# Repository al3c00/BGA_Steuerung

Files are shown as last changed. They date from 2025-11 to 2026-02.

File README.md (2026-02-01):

# BGA_Steuerung

## Übersicht:

Dieses Repository enthält Platine-Daten und Software zur Steuerung und Überwachung der Substratflüsse einer landwirtschaftlichen Biogasanlage. Angesteuert werden elektrische Motoren (Pumpen und Mischmotoren) mitels Schützrelais sowie pneumatisch gesteuerte Schieber mit einem 24V 5/2 Pneumatikventil.

## Funktion:

## Schnittstellen der Steuerungsplatine:

+ 24 Digitale Inputs für NPN-Sensoren (Signal aktiv wenn auf Masse gezogen)
+ 6 Analoge Inputs (Stromschleife 4-20mA)
+ 2 Analoge Inputs (0-5v)
+ 16 Digitale Outputs
+ UART, SPI, I2C, drahtlose Kommunikationsmöglichkeiten des Raspberry Pi 4
  
## Steuerung der Anlage:
### Sequenzen für Steuerung:
Das Programm lädt Sequenzen, die zu einem bestimmten Zeitpunkt abgespielt werden sollen. Der Benutzer ist frei in der Programmierung der Sequenzen. Diese werden in einer .txt-Datei gespeichert und bei allfälligem Neustart des Programms wieder aufgerufen. Jede Funktion wird in einem eigenen Thread ausgeführt
Es können folgende Funktionen verwendet werden:
|Funktionsname|Beschrieb|Parameter_int1|Parameter_int2|Parameter_string1|Parameter_string2|
|---|---|---|---|---|---|
|WAIT_MS|Stoppt die Ausführung der Sequenz indem der Thread mittels std::this_thread::sleep_for angehalten wird|Wartezeit in Millisekunden int|-|-|-|
|WAIT_S|Stoppt die Ausführung der Sequenz indem der Thread mittels std::this_thread::sleep_for angehalten wird|Wartezeit in Sekunden int|-|-|-|
|WAIT_MIN|Stoppt die Ausführung der Sequenz indem der Thread mittels std::this_thread::sleep_for angehalten wird|Wartezeit in Minuten int|-|-|-|
|WAIT_H|Stoppt die Ausführung der Sequenz indem der Thread mittels std::this_thread::sleep_for angehalten wird|Wartezeit in Stunden int|-|-|-|
|WAIT_UNTIL|Stoppt die Ausführung der Sequenz bis zu einer gewissen Tageszeit (HHMM). Der Thread wird mit std::this_thread::sleep_for angehalten und es wird alle 30 Sekunden überprüft, ob die Uhrzeit erreicht worden ist|Tageszeit Stunde int|Tageszeit Minute int|-|-|
|JUMP_TO|Springt zu einer bestimmten Position in der Sequenz und fährt dort weiter|Zielposition (0 bis n)|-|-|-|
|PROGRESS_IF_1|Die Ausführung der Sequenz wird angehalten bis eine bestimmte Bedingung erfüllt ist an **einem** Input erfüllt ist|int_Zustand, der zu erfüllen ist|-|Input, der abgefragt wird|-|
|PROGRESS_IF_2|Die Ausführung der Sequenz wird angehalten bis eine bestimmte Bedingung erfüllt ist an **zwei** Inputs erfüllt ist (siehe HW_Con::getDoubleInputState|int_Zustand, der zu erfüllen ist|-|Input, der abgefragt wird|Input, der abgefragt wird|
|GET_DIGITAL_INPUT|Der aktuelle Zustand eines digitalen Inputs wird abgefragt|-|-|Input, der abgefragt wird|-|
|GET_DOUBLE_DIGITAL_INPUT|Die Funktion "getDoubleInputState" wird verwendet, um die Sensorwerte eines mechanischen Bauteils, dass Stellung An und Aus überwacht (nicht nur eine von beiden) zu überprüfen|-|-|Input1, der abgefragt wird|Input2, der abgefragt wird|
|GET_ANALOG_INPUT|Der aktuelle Zustand eines analogen Inputs wird abgefragt|-|-|Input, der abgefragt wird|-|
|SET_DIGITAL_OUTPUT|Der Zustand eines digitalen Outputs wird unabhängig von seinem aktuellen Zustand gesetzt|Zustand, der gesetzt werden soll (0/1, eigentlich Bool)|-|Output, der gesetzt werden soll|-|
|SWITCH_DIGITAL_OUTPUT|Der Zustand eines digitalen Outputs wird abhängig von seinem aktuellen Zustand ins Gegenteil gesetzt|-|-|Output, der gesetzt werden soll|-|
|NOT_DEFINED|Wird verwendet, um Fehler abzufangen und die struct zu konstruieren

Die Funktionen in der .txt-Datei nutzen folgende Syntax:
|Objekt|Beschrieb|
|---|---|
|#Sequencename|Name der Sequenz. Dieser wird im Quellcode für die Zuordnung an verschiedensten Stellen benutzt.| 
|"{"|Markiert den Beginn der Sequenz|
|Funktionsname(Parameter1, ev. Parameter2)|Siehe die oben beschriebenen Funktionen oder im Quellcode Sequence_Handler.h|
|"}"|Markiert das Ende der Sequenz|

Alle Sequenzen werden in derselben Datei gespeichert.

## Software:
### Allgemein:
Das Programm läuft auf einem Raspberry Pi 4, welcher mittel I2C mit den IO-Expandern auf der Platine kommuniziert. Die Kommunikation übernimmt eine Klasseninstanz von HW_Con. Die grafische Darstellung übernimmt die Klasse GUI, für z.B.unterschiedliche Ebenen können mehrere Instanzen erzeugt werden. Für das Rendering wird SDL2 genutzt. Es wird auf eine Abstrahierung des Quellcodes geachtet, viele Positionen der Elemente auf dem Display können in der dazugehörigen .txt-Datei angepasst und in der Software während Laufzeit neu geladen werden.

### GUI:
Es existiert mindestens eine Instaz der Klasse GUI. Damit können Bilder geladen und angezeigt und Text ausgegeben werden. Alle grafischen Elemente werden in einer std::map mit einem string-key referenziert. Es lassen sich vordefinierte Positionen in einem .txt-Dokument speichern und laden.

### HW_Con:
Von dieser Klasse darf nur eine Instanz erzeugt werden. Mittels I2C kommuniziert der PI mit den PCF8574 auf der Platine. Die einzelnen Inputs/Outputs sind mit ihren 7-Bit I2C Adressen der Chips sowie dem Port mit string-Namen in einer Map referenziert. *Beispiel: D_Out_0 --> dec35,p0.* Für jeden Input/Output existiert eine struct "IO_Object". Die Inputs werden im Main-Loop regelmässig neu abgefragt. Bei den Outputs wird der **Soll-Zustand** in dieser struct gespeichert und übermittelt. Der Ist-Zustand kann nicht abgefragt werden.

### Sequence_Handler:
Von dieser Klasse darf nur eine Instanz erzeugt werden. Sie lädt, speichert und organisert alle Sequenzen und überwacht deren Ausführung und gegebenenfalls Bearbeitung.

## Weiteres
Verbesserungspotenzial:
+ GND Pins bei I2C und UART Terminals vergessen
+ Sicherheit der digitalen Outputs verbessern (z.B.: blockieren der Stromversorgung aller Relais bis zum Zeitpunkt der explizit gewünschten Freigabe
+ Schöneres Layout der Platine
+ Aufbauposition des Raspberry optimieren
+ Pin Header besser zu Montageposition des RPI anpassen
+ Diverses mehr

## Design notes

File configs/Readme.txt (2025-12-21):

Sequences
WAIT(int-->wait time in ms);
PROGRESS_IF_1(int-->should_be_state, string-->input to check);
PROGRESS_IF_2(int-->should_be_state, string-->input one to check, string-->input two to check);
SWITCH_DIGITAL_OUTPUT(string-->output to switch);

//Finish lines with ;

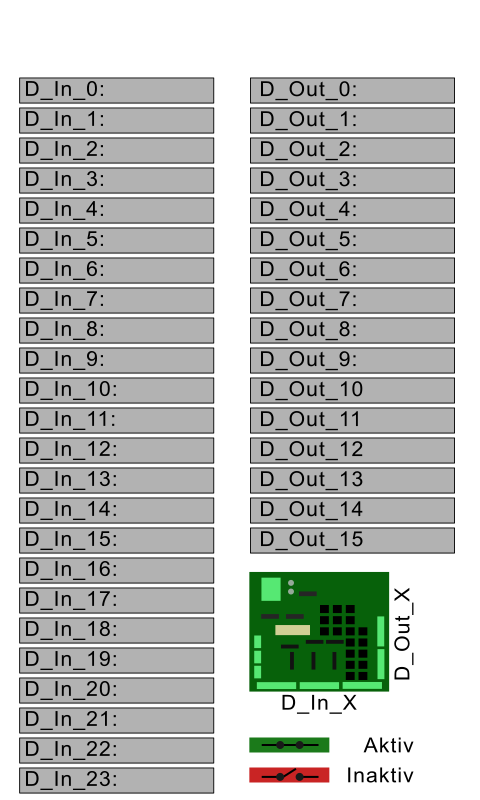
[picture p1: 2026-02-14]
resource/schema_IO_v1.png

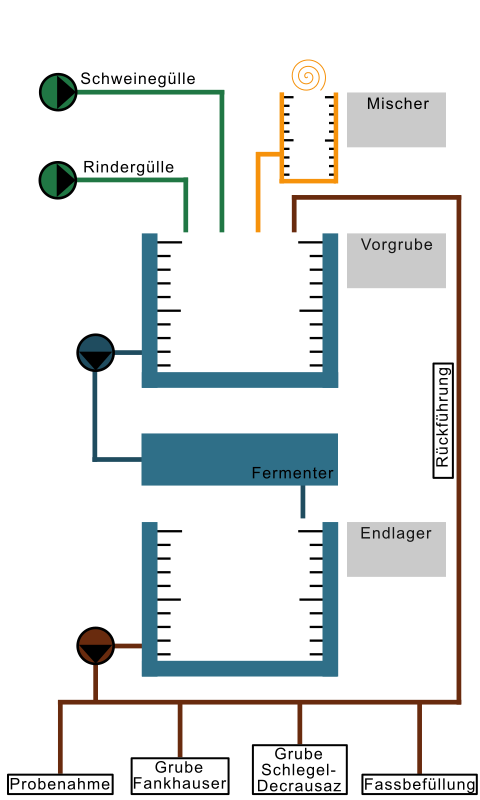
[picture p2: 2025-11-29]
resource/schema_bga_v3.png

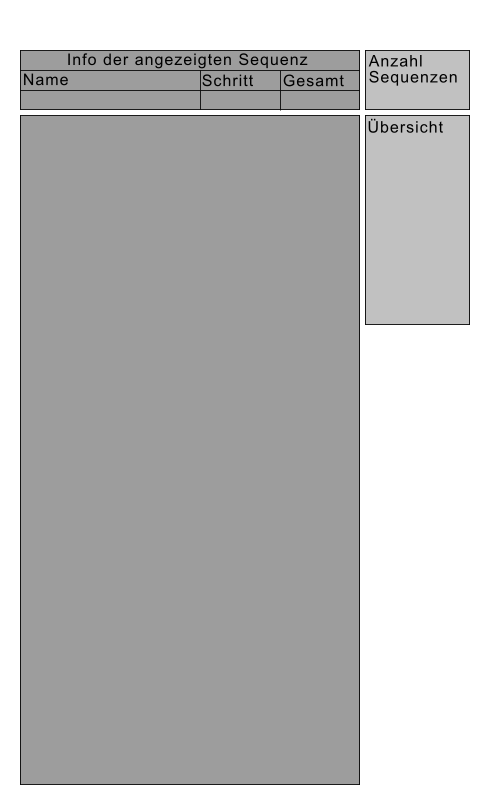
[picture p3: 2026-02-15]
resource/Sequenzuebersicht.png

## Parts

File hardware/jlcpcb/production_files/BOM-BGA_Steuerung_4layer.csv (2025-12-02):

Comment | Designator | Footprint | LCSC | Quantity
0.1uF | C10,C11,C12,C13,C14,C15,C34 | C_0603_1608Metric | C1590 | 7
0.1uf | C16,C17,C18,C19,C20,C21,C22,C23,C24,C25,C26,C27,C28,C29,C30,C31,C32,C33 | C_0603_1608Metric | C1590 | 18
1.8k | R81,R87,R91,R94,R96,R98 | R_0603_1608Metric | C4177 | 6
100nF | C35,C36,C37 | CP_Elec_4x5.4 | C271438 | 3
10k | R117,R118,R119,R120,R121,R122,R123,R124,R125,R126,R127,R128,R129,R130 | R_0603_1608Metric | C15401 | 14
10nF | C39,C40 | C_0603_1608Metric | C1589 | 2
10uF | C3 | C_Elec_4x5.4 | C3343 | 1
150 | R2,R4 | R_0603_1608Metric | C22808 | 2
1N5824 | D2,D3,D6 | D_A-405_P12.70mm_Horizontal | C508482 | 3
1k | R10,R12,R14,R16,R18,R20,R22,R29,R30,R31,R32,R33,R34,R37,R38,R45,R46,R47,R48,R49,R50,R53,R54,R8,R85,R86 | R_0603_1608Metric | C14676 | 26
200 | R100,R71,R72,R73,R74,R75,R99 | R_0603_1608Metric | C8218 | 7
220nF | C38,C41,C42,C43,C44 | C_0603_1608Metric | C1606 | 5
220uF | C6,C7,C9 | C_Elec_8x10.2 | C3340 | 3
250 | R79,R82,R84,R88,R90,R92 | R_0805_2012Metric | C2828827 | 6
2k | R55,R56,R57,R58,R59,R60,R61,R62,R63,R64,R65,R66,R67,R68,R69,R70 | R_0603_1608Metric | C22975 | 16
33uH | L1,L2,L3 | L_Chilisin_BMRF00101040 | C6364680 | 3
4.7k | R5,R6,R77,R78,R80,R83,R89,R93,R95,R97 | R_0603_1608Metric | C23162 | 10
470uF | C1,C2 | C_Elec_10x10.2 | C3351 | 2
500 | R1 | R_0805_2012Metric | C2828857 | 1
510 | R101,R102,R103,R104,R105,R106,R107,R108,R109,R11,R110,R111,R112,R113,R114,R115,R116,R13,R15,R17,R19,R21,R23,R24,R25,R26,R27,R28,R35,R36,R39,R40,R41,R42,R43,R44,R51,R52,R7,R9 | R_0603_1608Metric | C23193 | 40
680uF | C4,C5,C8 | CP_Elec_5x5.4 | C3337 | 3
75 | R3 | R_0603_1608Metric | C4275 | 1
LED_Green | D48,D49,D50,D53 | L_0603_1608Metric | C118334 | 4
LED_Green | D1,D4,D5,D7 | LED_0805_2012Metric | C84260 | 4
LED_Red | D51,D52,D54 | L_0603_1608Metric | C2286 | 3
Raspberry_Pi_4b_GPIO_Header | U4 | PinHeader_2x20_P2.54mm_Vertical | C3326996 | 1
TCA9406DCUR | U35 | VSSOP-8_2.3x2mm_P0.5mm | C840107 | 1
Conn_01x24_Socket | J5 | Connector PTSA 24Pos Pitch=2.5mm |  | 1
2N4401 | Q5 | TO-92_Inline_Wide_EBC |  | 1
2N4401 | Q2 | TO-92_Inline_Wide_EBC |  | 1
2N4401 | Q13 | TO-92_Inline_Wide_EBC |  | 1
4N35 | U28 | DIP-6_W7.62mm |  | 1
LED | D19 | D_0603_1608Metric |  | 1
LED | D58 | D_0603_1608Metric |  | 1
LED | D22 | D_0603_1608Metric |  | 1
LED | D65 | D_0603_1608Metric |  | 1
2N4401 | Q14 | TO-92_Inline_Wide_EBC |  | 1
Conn_01x01_Pin | J20 | PinHeader_1x01_P1.00mm_Vertical |  | 1
LED | D25 | D_0603_1608Metric |  | 1
LED | D28 | D_0603_1608Metric |  | 1
4N35 | U8 | DIP-6_W7.62mm |  | 1
Conn_01x16_Socket | J6 | 1989887 |  | 1
1N4148 | D44 | D_DO-35_SOD27_P7.62mm_Horizontal |  | 1
LED | D13 | D_0603_1608Metric |  | 1
TPS26610 | U42 | SOT-23-8 |  | 1
2N4401 | Q11 | TO-92_Inline_Wide_EBC |  | 1
4N35 | U9 | DIP-6_W7.62mm |  | 1
4N35 | U25 | DIP-6_W7.62mm |  | 1
Screw_Terminal_01x02 | J22 | 691137710002 |  | 1
LED | D12 | D_0603_1608Metric |  | 1
Heatsink | HS1 | Heatsink_TO-220_V6560W |  | 1
Conn_01x01_Pin | J19 | PinHeader_1x01_P1.00mm_Vertical |  | 1
AZ9571-1C-12DSE | K7 | RELAY6_AZ9571-1C-12DSE_AMZ |  | 1
1990009 | J15 | 1990009 |  | 1
2N4401 | Q15 | TO-92_Inline_Wide_EBC |  | 1
~ | U5 | DIP-16_W7.62mm |  | 1
4N35 | U11 | DIP-6_W7.62mm |  | 1
LED | D64 | D_0603_1608Metric |  | 1
LED | D69 | D_0603_1608Metric |  | 1
1990009 | J14 | 1990009 |  | 1
1N4148 | D36 | D_DO-35_SOD27_P7.62mm_Horizontal |  | 1
LM2596T-5 | U3 | TO-220-5_P3.4x3.7mm_StaggerOdd_Lead3.8mm_Vertical |  | 1
LED | D14 | D_0603_1608Metric |  | 1
LED | D16 | D_0603_1608Metric |  | 1
TPS26610 | U39 | SOT-23-8 |  | 1
LED | D31 | D_0603_1608Metric |  | 1
1N4148 | D35 | D_DO-35_SOD27_P7.62mm_Horizontal |  | 1
AZ9571-1C-12DSE | K12 | RELAY6_AZ9571-1C-12DSE_AMZ |  | 1
LED | D26 | D_0603_1608Metric |  | 1
Conn_01x01_Pin | J21 | PinHeader_1x01_P1.00mm_Vertical |  | 1
1990009 | J13 | 1990009 |  | 1
4N35 | U19 | DIP-6_W7.62mm |  | 1
AZ9571-1C-12DSE | K13 | RELAY6_AZ9571-1C-12DSE_AMZ |  | 1
2N4401 | Q9 | TO-92_Inline_Wide_EBC |  | 1
1N4148 | D40 | D_DO-35_SOD27_P7.62mm_Horizontal |  | 1
1990009 | J16 | 1990009 |  | 1
LED | D21 | D_0603_1608Metric |  | 1
AZ9571-1C-12DSE | K2 | RELAY6_AZ9571-1C-12DSE_AMZ |  | 1
LED | D67 | D_0603_1608Metric |  | 1
LED | D29 | D_0603_1608Metric |  | 1
~ | U31 | DIP-16_W7.62mm |  | 1
Conn_01x01_Pin | J18 | PinHeader_1x01_P1.00mm_Vertical |  | 1
Heatsink | HS2 | Heatsink_TO-220_V6560W |  | 1
4N35 | U12 | DIP-6_W7.62mm |  | 1
LED | D68 | D_0603_1608Metric |  | 1
~ | U33 | DIP-16_W7.62mm |  | 1
2N4401 | Q4 | TO-92_Inline_Wide_EBC |  | 1
1N4148 | D33 | D_DO-35_SOD27_P7.62mm_Horizontal |  | 1
TPS26610 | U43 | SOT-23-8 |  | 1
1N4148 | D34 | D_DO-35_SOD27_P7.62mm_Horizontal |  | 1
AZ9571-1C-12DSE | K10 | RELAY6_AZ9571-1C-12DSE_AMZ |  | 1
AZ9571-1C-12DSE | K9 | RELAY6_AZ9571-1C-12DSE_AMZ |  | 1
1N4148 | D37 | D_DO-35_SOD27_P7.62mm_Horizontal |  | 1
1N4148 | D46 | D_DO-35_SOD27_P7.62mm_Horizontal |  | 1
~ | U44 | DIP-16_W7.62mm |  | 1
4N35 | U6 | DIP-6_W7.62mm |  | 1
LM2596T-3.3 | U2 | TO-220-5_P3.4x3.7mm_StaggerOdd_Lead3.8mm_Vertical |  | 1
2N4401 | Q12 | TO-92_Inline_Wide_EBC |  | 1
LED | D27 | D_0603_1608Metric |  | 1
Conn_01x01_Pin | J23 | PinHeader_1x01_P1.00mm_Vertical |  | 1
ADS1115IDGSR | U36 | TSSOP-10_3x3mm_P0.5mm |  | 1
1N4148 | D43 | D_DO-35_SOD27_P7.62mm_Horizontal |  | 1
LED | D10 | D_0603_1608Metric |  | 1
LED | D61 | D_0603_1608Metric |  | 1
LED | D66 | D_0603_1608Metric |  | 1
AZ9571-1C-12DSE | K3 | RELAY6_AZ9571-1C-12DSE_AMZ |  | 1
LED | D17 | D_0603_1608Metric |  | 1
4N35 | U18 | DIP-6_W7.62mm |  | 1
LED | D18 | D_0603_1608Metric |  | 1
LED | D15 | D_0603_1608Metric |  | 1
1N4148 | D41 | D_DO-35_SOD27_P7.62mm_Horizontal |  | 1
2N4401 | Q7 | TO-92_Inline_Wide_EBC |  | 1
~ | U34 | DIP-16_W7.62mm |  | 1
1N4148 | D38 | D_DO-35_SOD27_P7.62mm_Horizontal |  | 1
4N35 | U21 | DIP-6_W7.62mm |  | 1
AZ9571-1C-12DSE | K11 | RELAY6_AZ9571-1C-12DSE_AMZ |  | 1
LED | D11 | D_0603_1608Metric |  | 1
AZ9571-1C-12DSE | K1 | RELAY6_AZ9571-1C-12DSE_AMZ |  | 1
2N4401 | Q8 | TO-92_Inline_Wide_EBC |  | 1
4N35 | U14 | DIP-6_W7.62mm |  | 1
4N35 | U16 | DIP-6_W7.62mm |  | 1
Conn_01x24_Socket | J3 | Connector PTSA 24Pos Pitch=2.5mm |  | 1
1990009 | J11 | 1990009 |  | 1
4N35 | U17 | DIP-6_W7.62mm |  | 1
LED | D59 | D_0603_1608Metric |  | 1
2N4401 | Q16 | TO-92_Inline_Wide_EBC |  | 1
~ | U22 | DIP-16_W7.62mm |  | 1
ADS1115IDGSR | U37 | TSSOP-10_3x3mm_P0.5mm |  | 1
Power_Rasperry | J2 | TerminalBlock_MetzConnect_Type055_RT01502HDWU_1x02_P5.00mm_Horizontal |  | 1
Screw_Terminal_01x02 | J17 | 691137710002 |  | 1
AZ9571-1C-12DSE | K14 | RELAY6_AZ9571-1C-12DSE_AMZ |  | 1
1N4148 | D47 | D_DO-35_SOD27_P7.62mm_Horizontal |  | 1
1N4148 | D32 | D_DO-35_SOD27_P7.62mm_Horizontal |  | 1
AZ9571-1C-12DSE | K5 | RELAY6_AZ9571-1C-12DSE_AMZ |  | 1
LED | D30 | D_0603_1608Metric |  | 1
1N4148 | D42 | D_DO-35_SOD27_P7.62mm_Horizontal |  | 1
4N35 | U20 | DIP-6_W7.62mm |  | 1
Conn_01x01_Pin | J24 | PinHeader_1x01_P1.00mm_Vertical |  | 1
1N4148 | D39 | D_DO-35_SOD27_P7.62mm_Horizontal |  | 1
4N35 | U29 | DIP-6_W7.62mm |  | 1
2N4401 | Q6 | TO-92_Inline_Wide_EBC |  | 1
4N35 | U15 | DIP-6_W7.62mm |  | 1
4N35 | U23 | DIP-6_W7.62mm |  | 1
2N4401 | Q1 | TO-92_Inline_Wide_EBC |  | 1
4N35 | U7 | DIP-6_W7.62mm |  | 1
1990012 | J10 | 1990012 |  | 1
Conn_01x24_Socket | J4 | Connector PTSA 24Pos Pitch=2.5mm |  | 1
4N35 | U30 | DIP-6_W7.62mm |  | 1
2N4401 | Q3 | TO-92_Inline_Wide_EBC |  | 1
LED | D70 | D_0603_1608Metric |  | 1
TPS26610 | U38 | SOT-23-8 |  | 1
4N35 | U27 | DIP-6_W7.62mm |  | 1
1N4148 | D45 | D_DO-35_SOD27_P7.62mm_Horizontal |  | 1
AZ9571-1C-12DSE | K6 | RELAY6_AZ9571-1C-12DSE_AMZ |  | 1
1990012 | J9 | 1990012 |  | 1
4N35 | U24 | DIP-6_W7.62mm |  | 1
4N35 | U10 | DIP-6_W7.62mm |  | 1
Heatsink | HS3 | Heatsink_TO-220_V6560W |  | 1
LED | D8 | D_0603_1608Metric |  | 1
LED | D57 | D_0603_1608Metric |  | 1
Screw_Terminal_0,5-6,0mm2 | J1 | PCB_terminal_block_1932588 |  | 1
4N35 | U26 | DIP-6_W7.62mm |  | 1
LED | D23 | D_0603_1608Metric |  | 1
TPS26610 | U41 | SOT-23-8 |  | 1
LED | D60 | D_0603_1608Metric |  | 1
Screw_Terminal_0,5-6,0mm2 | J8 | PCB_terminal_block_1932588 |  | 1
~ | U32 | DIP-16_W7.62mm |  | 1
LED | D62 | D_0603_1608Metric |  | 1
LED | D24 | D_0603_1608Metric |  | 1
LED | D20 | D_0603_1608Metric |  | 1
LED | D55 | D_0603_1608Metric |  | 1
4N35 | U13 | DIP-6_W7.62mm |  | 1
Conn_01x06_Pin | J25 | PinHeader_1x06_P2.54mm_Vertical |  | 1
LED | D9 | D_0603_1608Metric |  | 1
TPS26610 | U40 | SOT-23-8 |  | 1
LM2596T-5 | U1 | TO-220-5_P3.4x3.7mm_StaggerOdd_Lead3.8mm_Vertical |  | 1
AZ9571-1C-12DSE | K16 | RELAY6_AZ9571-1C-12DSE_AMZ |  | 1
2N4401 | Q10 | TO-92_Inline_Wide_EBC |  | 1
AZ9571-1C-12DSE | K15 | RELAY6_AZ9571-1C-12DSE_AMZ |  | 1
1990009 | J12 | 1990009 |  | 1
LED | D63 | D_0603_1608Metric |  | 1
LED | D56 | D_0603_1608Metric |  | 1
Conn_01x16_Socket | J7 | 1989887 |  | 1
AZ9571-1C-12DSE | K8 | RELAY6_AZ9571-1C-12DSE_AMZ |  | 1
AZ9571-1C-12DSE | K4 | RELAY6_AZ9571-1C-12DSE_AMZ |  | 1
TL2230OAF140 | SW5 | TL2230OAF140 |  | 1
TL2230OAF140 | SW2 | TL2230OAF140 |  | 1
TL2230OAF140 | SW3 | TL2230OAF140 |  | 1
TL2230OAF140 | SW4 | TL2230OAF140 |  | 1
PEC11R-4220K-S0024 | SW1 | PEC11R |  | 1
RP | RP | RP_PI_4B |  | 1
4.3_Display | DP | 4.3_Display |  | 1

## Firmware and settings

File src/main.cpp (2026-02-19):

#include <iostream>
#include <chrono>
#include <thread>


#include "Log.h"
#include "Render.h"
#include "defines.h"
#include "GUI.h"
#include "HW_Con.h"
#include "Sequence_Handler.h"


int main()
{
	std::string log_origin = "MAIN";//Create such a string variable in every space needed with an name which tells, from where the logger was called
	Log logger("/logs/logs.txt");

	SDL_Window* window;

	

	//Initialize SDL
	if (SDL_InitSubSystem(NULL) < 0)//Return Value: 0 on success, negative value on failure
	{
		logger.writeLog(LogLevel::ERROR, log_origin + " SDL_INIT", SDL_GetError());
		std::cout << SDL_GetError() << std::endl;
	}

	int gui_state = 1; //used to iterate over the different GUIs
	int nmbr_of_guis = 3;//Ammount of used guis 

	//Initialize IMG
	//According to description, no return error check, because the function return the flag-values
	IMG_Init(IMG_INIT_JPG | IMG_INIT_PNG);

	if (TTF_Init() < 0)
	{
		logger.writeLog(LogLevel::ERROR, log_origin + " TTF_INIT", TTF_GetError());
	}

	//Create Window
	window = SDL_CreateWindow("BGA_Steuerung", 0, 0, 480, 800, SDL_WINDOW_FULLSCREEN);
	if (!window)
	{
		logger.writeLog(LogLevel::ERROR, log_origin + " SDL_CREATE_WINDOW", SDL_GetError());
		std::cout << SDL_GetError() << std::endl;
	}

	//Create a renderer, that is used by every GUI instance
	Render renderer(&logger, window);
	
	//Create GUI instance (main gui)
	GUI system_diagram(&logger, &renderer);

	GUI sequence_overview(&logger, &renderer);

	GUI io_overview(&logger, &renderer);

	//Create Hardware-handling class instance
	auto hw = std::make_shared<HW_Con>(&logger);

	hw->loadDigitalInputAdresses("/configs/D_In_config.txt");
	hw->loadAnalogInputAdresses("/configs/A_In_config.txt");
	hw->loadDigitalOutputAdresses("/configs/D_Out_config.txt");
	hw->loadIOMapConfig("/configs/HW_IO_map_config.txt");
	hw->initialisePCBRelayState();

	Sequence_Handler sqh(&logger, hw);
	


	sqh.loadSequences("/sequences");
	sqh.startSequences();
	
	

	system_diagram.loadFont("ARIAL_Black", "/fonts/arial.ttf", 0, 0, 0);
	system_diagram.loadTexture("Circular_Arrow", "/resource/circle_arrow.png");
	system_diagram.loadTexture("Schema", "/resource/schema_bga_v3.png");
	system_diagram.loadTexture("HALT_Symbol", "/resource/halt_symbol.png");
	system_diagram.loadTexture("Schieber_Geschlossen", "/resource/schieber_geschlossen.png");
	system_diagram.loadTexture("Schieber_Offen", "/resource/schieber_offen.png");
	system_diagram.loadTexture("Schieber_Unbekannt", "/resource/schieber_unbekannt.png");




	sequence_overview.loadFont("ARIAL_Black", "/fonts/arial.ttf", 0, 0, 0);
	sequence_overview.loadTexture("Seq_Liste", "/resource/Sequenzuebersicht.png");
	sequence_overview.loadTexture("Dreieck_Rechts", "/resource/dreieck_rechts.png");
	sequence_overview.loadTexture("Dreieck_Links", "/resource/dreieck_links.png");
	sequence_overview.loadTexture("Sequenz_Play_Pause", "/resource/play_pause.png");
	sequence_overview.loadTexture("Sequenz_Reload", "/resource/reload.png");

	io_overview.loadFont("ARIAL_Black", "/fonts/arial.ttf", 0, 0, 0);
	io_overview.loadTexture("IO_Liste", "/resource/schema_IO_v1.png");
	io_overview.loadTexture("IO_Aktiv", "/resource/stromkreis_geschlossen_gruen.png");
	io_overview.loadTexture("IO_Inaktiv", "/resource/stromkreis_offen_rot.png");


	std::chrono::system_clock::time_point now = std::chrono::system_clock::now();
	std::chrono::system_clock::time_point last_frame = std::chrono::system_clock::now();
	std::chrono::duration<double, std::milli> total_time_last_frame;
	int target_fps = 30;

	auto time = std::chrono::system_clock::now();
	std::time_t current_time; 
	std::string str_current_time;


	

	//Main loop
	//{
	//	clear renderer
	//	draw things in backbuffer, from back to front
	//	show things
	//}

	
	
	int rotation = 0;
	int asked_sequence = 0;
	int y_corr = 0;
	bool io_state = false;


	do
	{
		

		now = std::chrono::system_clock::now();
		total_time_last_frame = now - last_frame;
		


		hw->refreshDigitalInputStates();


	
		
		

		if (total_time_last_frame.count() > static_cast<float>(1000) /target_fps)
		{	

			


			//Iterate over GUI state
			if (hw->getButton2Press())
			{
				gui_state++;
			
				if (gui_state > nmbr_of_guis - 1)
				{
					gui_state = 0;
				}
			}

		
			/*std::cout << "Button4: " << hw->getDigitalGPIOState(GPIO_BCM_BUTTON4) << std::endl;
			std::cout << "EncoderA: " << hw->getDigitalGPIOState(GPIO_BCM_ENCODER_A) << std::endl;
			std::cout << "EncoderB: " << hw->getDigitalGPIOState(GPIO_BCM_ENCODER_B) << std::endl;*/

			//Get system time
			time = now;
			current_time = std::chrono::system_clock::to_time_t(time);
			str_current_time = std::ctime(&current_time);
			//std::ctime inserts a newline at the end of the time data. Remove it with pop_back
			str_current_time.pop_back();

			renderer.clearRender();

				if (gui_state == 0)
				{


					if (hw->getEncoderPush())
					{
						system_diagram.switchCursorState();
					}
					system_diagram.prepareCursor();

					system_diagram.moveCursor(hw->getEncoderDirection());

				
					system_diagram.drawBackGroundColor(205, 205, 205);
					system_diagram.drawVisualElement(0, 0, 480, 800, "Schema", false);

					//Info Elements: Time and date, FPS, ms/frame
					system_diagram.drawVisualElement(0, 0, 480, 30, 245, 245, 245, false);
					system_diagram.drawText_l(231, 9, "FPS: " + std::to_string(target_fps), "ARIAL_Black");
					system_diagram.drawText_r(473, 9, "Time(ms)/frame: " + std::to_string((int)total_time_last_frame.count()), "ARIAL_Black");
					system_diagram.drawText_l(7, 9, str_current_time, "ARIAL_Black");
				

					system_diagram.drawVisualElement(78, 98, 20, 20, rotation, "Circular_Arrow", true);//Pumpe1
					system_diagram.drawVisualElement(78, 186, 20, 20, rotation, "Circular_Arrow", false);//Pumpe2
					system_diagram.drawVisualElement(111, 366, 20, 20, rotation, "Circular_Arrow", false);//Pumpe3
					system_diagram.drawVisualElement(213, 198, 20, 20, hw->getDoubleInputState("D_In_0", "D_In_1"), false);//Schieber_Rinderguelle
					system_diagram.drawVisualElement(261, 145, 20, 20, 270, "Schieber_Geschlossen", false);//Schieber_Mischer
					system_diagram.drawVisualElement(52, 716, 20, 20, "Schieber_Geschlossen", true);//Schieber_Probenahme
					system_diagram.drawVisualElement(172, 716, 20, 20, "Schieber_Geschlossen",false);//Schieber_Grube_Fankhauser
					system_diagram.drawVisualElement(291, 716, 20, 20, "Schieber_Geschlossen", false);//Schieber_Grube_Schlegel
					system_diagram.drawVisualElement(411, 716, 20, 20, "Schieber_Geschlossen", true);//Schieber_Fassbefuellung
					system_diagram.drawVisualElement(450, 659, 20, 20, "Schieber_Offen", false);//Schieber_Rueckfuehrung

					//system_diagram.drawPreloadedTexture(80, 186, 15, 15, rotation, "Arrow_Active");
					//system_diagram.drawText_l(50, 200, "Hello World", "ARIAL_Black");
					//system_diagram.drawText_l(80, 400, "Hello World", "ARIAL_Black");
					system_diagram.drawText_l(349, 112, std::to_string(4850) + "kg", "ARIAL_Black");
					system_diagram.drawText_l(349, 130, std::to_string(75) + "%", "ARIAL_Black");
				
				

					system_diagram.drawCursor();

				}

				//Sequence overview
				else if (gui_state == 1)
				{
					if (hw->getEncoderPush())
					{
						sequence_overview.switchCursorState();
					}
					sequence_overview.prepareCursor();
					
					if (hw->getButton1Press())
					{
						sqh.switchThroughSequences();
					}

					sequence_overview.drawBackGroundColor(205, 205, 205);
					sequence_overview.drawVisualElement(0, 0, 480, 800, "Seq_Liste", false);


					//Info Elements: Time and date, FPS, ms/frame
					sequence_overview.drawVisualElement(0, 0, 480, 30, 205, 205, 205, false);
					sequence_overview.drawText_l(231, 9, "FPS: " + std::to_string(target_fps), "ARIAL_Black");
					sequence_overview.drawText_r(473, 9, "Time(ms)/frame: " + std::to_string((int)total_time_last_frame.count()), "ARIAL_Black");
					sequence_overview.drawText_l(7, 9, str_current_time, "ARIAL_Black");

					//Sequenzinfo
					sequence_overview.drawText_l(22, 92, sqh.getSequenceInfo_Name(), "ARIAL_Black");
					sequence_overview.drawText_l(203, 92, sqh.getSequenceInfo_CurrentStep(), "ARIAL_Black");
					sequence_overview.drawText_l(282, 92, sqh.getSequenceInfo_TotalSteps(), "ARIAL_Black");

					//Sequenzanzahl
					sequence_overview.drawText_l(368, 92, std::to_string(sqh.getNmbrOfRunningSequences()), "ARIAL_Black");


					sequence_overview.drawList_l(23, 120, 22, 270, 660, hw->getButton3Press(), hw->getButton4Press(), sqh.getSequenceInfo_Functions(), "ARIAL_Black", false);


					for (int i = 0; i < sqh.getNmbrOfRunningSequences(); i++)
					{
						//Draw text for every loaded sequence. Offset the y-position for every sequence
						/*sequence_overview.drawText_l(305, 160 + i* 20, "Sequence " + std::to_string(i) + ": " + std::to_string(sqh.getExecutionStep(sqh.getSequenceName(i))), "ARIAL_Black");
						sequence_overview.drawText_l(305, 160 + i *20, "Sequence " + std::to_string(i) + ": " + std::to_string(sqh.getExecutionStep(sqh.getSequenceName(i))), "ARIAL_Black");*/

						//sequence_overview.drawList_l(368, 138+ i*40, 20, { sqh.getSequenceName(i), std::to_string(sqh.getExecutionStep(sqh.getSequenceName(i)))}, "ARIAL_Black");
					}


					sequence_overview.drawCursor();
					
				}

				//io_overview
				else if (gui_state == 2)
				{
					if (hw->getEncoderPush())
					{
						io_overview.switchCursorState();
					}
					io_overview.prepareCursor();


					io_overview.drawBackGroundColor(225, 225, 225);
					io_overview.drawVisualElement(0, 0, 480, 800, "IO_Liste", false);

					//Info Elements: Time and date, FPS, ms/frame
					io_overview.drawVisualElement(0, 0, 480, 30, 245, 245, 245, false);
					io_overview.drawText_l(231, 9, "FPS: " + std::to_string(target_fps), "ARIAL_Black");
					io_overview.drawText_r(473, 9, "Time(ms)/frame: " + std::to_string((int)total_time_last_frame.count()), "ARIAL_Black");
					io_overview.drawText_l(7, 9, str_current_time, "ARIAL_Black");

					io_overview.drawText_l(10, 40, "Digitale Inputs: ", "ARIAL_Black");
					io_overview.drawText_l(300, 40, "Digitale Outputs: ", "ARIAL_Black");

					/*io_overview.drawVisualElement(295, 725, 100, 55, 200, 200, 200, false);
					io_overview.drawText_l(300, 730, "Rot = Inaktiv", "ARIAL_Black", 255, 0, 0);
					io_overview.drawText_l(300, 755, "Gruen = Aktiv", "ARIAL_Black", 0, 255, 0);*/

					
					
					

					for (int i = 0; i < 24; i++)
					{
						std::string input_name = "D_In_" + std::to_string(i);
						io_state = hw->getDigitalInputState(input_name);
						io_overview.drawVisualElement(120, 83 + y_corr, 80, 15, (io_state ? "IO_Inaktiv" : "IO_Aktiv"), false);
						y_corr += 30;

					}


					y_corr = 0;

					for (int i = 0; i < 16; i++)
					{
						std::string output_name = "D_Out_" + std::to_string(i);
						io_state = hw->getDigitalOutputState(output_name);
						io_overview.drawVisualElement(370, 83 + y_corr, 80, 15, (io_state ? "IO_Aktiv" : "IO_Inaktiv"), false);
						y_corr += 30;

					}
					
					y_corr = 0;

				}

			renderer.Show();

			//SDL_Delay(15000);

			rotation++;
			if (rotation > 360)
			{
				rotation = 0;
			}

			last_frame = now;
		}

		

	} while (true);



	logger.writeLog(LogLevel::INFO, log_origin, "SUCCESSFUL");

	return 0;
}

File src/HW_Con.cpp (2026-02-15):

#include "HW_Con.h"

HW_Con::HW_Con(Log* logger)
{
	m_p_logger = logger;
	m_log_origin = "HW_Handle";


	m_PCF_IO_32 = wiringPiI2CSetupInterface("/dev/i2c-1", 32);
	m_PCF_IO_33 = wiringPiI2CSetupInterface("/dev/i2c-1", 33);
	m_PCF_IO_34 = wiringPiI2CSetupInterface("/dev/i2c-1", 34);
	m_PCF_IO_35 = wiringPiI2CSetupInterface("/dev/i2c-1", 35);
	m_PCF_IO_36 = wiringPiI2CSetupInterface("/dev/i2c-1", 36);

	wiringPiSetupGpio();
	
	
	pinMode(GPIO_BCM_ENCODER_A, INPUT);
	pinMode(GPIO_BCM_ENCODER_B, INPUT);
	pinMode(GPIO_BCM_ENCODER_PUSH, INPUT);

	pinMode(GPIO_BCM_BUTTON4, INPUT);
	pinMode(GPIO_BCM_BUTTON3, INPUT);
	pinMode(GPIO_BCM_BUTTON2, INPUT);
	pinMode(GPIO_BCM_BUTTON1, INPUT);


	m_flag_encoder_a = false;
	m_flag_encoder_b = false;
	m_flag_encoder_push = false;

	m_flag_button4 = false;
	m_flag_button3 = false;
	m_flag_button2 = false;
	m_flag_button1 = false;
	

	m_direction_has_been_used = false;
	m_encoder_direction = 0;
	

	std::thread(&HW_Con::encoder_handling,this, std::ref(m_encoder_direction), std::ref(m_direction_has_been_used)).detach();

}

int HW_Con::getEncoderDirection()
{
	int value = m_encoder_direction;
	m_encoder_direction = 0;
	m_direction_has_been_used = true;
	return value;
}

void HW_Con::encoder_handling(int& r_m_encoder_direction, bool& r_m_direction_has_been_used)
{
	int value = 0;
	while (true)
	{
		if(r_m_direction_has_been_used)

		if (!digitalRead(GPIO_BCM_ENCODER_A) && m_flag_encoder_a == false)
		{
			m_flag_encoder_a = true;
			
		}
		if (m_flag_encoder_a == true && m_flag_encoder_b == false)
		{
			m_encoder_b = digitalRead(GPIO_BCM_ENCODER_B);
			m_flag_encoder_b = true;
		}

		if (digitalRead(GPIO_BCM_ENCODER_A) && m_flag_encoder_a == true && digitalRead(GPIO_BCM_ENCODER_B) && m_flag_encoder_b == true)
		{
			if (m_encoder_b)
			{
				r_m_encoder_direction = 1;
				//std::cout << "Direction = +" << std::endl;
			}
			if (!m_encoder_b)
			{
				r_m_encoder_direction = -1;
				//std::cout << "Direction = -" << std::endl;
			}

			m_flag_encoder_a = false;
			m_flag_encoder_b = false;
			r_m_direction_has_been_used = false;
			std::this_thread::sleep_for(std::chrono::milliseconds(100));
		}



		
	}
}

void HW_Con::loadDigitalInputAdresses(std::string path)
{
	std::string temp;
	std::string single_character;
	std::string object_name;

	enum struct VARIANTS { PCF_ADRESSE = 0, PORT = 1 } variants;

	std::ifstream object_position_file(m_getProjectDirPath() + path);
	object_position_file.seekg(0, object_position_file.end);
	int length = object_position_file.tellg();
	object_position_file.seekg(0, object_position_file.beg);

	char* buffer = new char[length];

	m_p_logger->writeLog(LogLevel::INFO, m_log_origin + " LOAD_DIGITALINPUT_DATA", "Reading: " + std::to_string(length) + " characters");

	object_position_file.read(buffer, length);

	object_position_file.close();

	//Unsafe, file could be corrupted!!
	for (int i = 0; i < length; i++)
	{
		single_character = buffer[i];

		if (single_character != "#" && single_character != "{" && single_character != "}" && single_character != "," && single_character != "\n" && single_character != "\r")
		{
			temp.append(single_character);
		}

		//Check if a variant code word had been read (dec for PCF8574 7-Bit Adresse, p for the Port). If yes clear string and prepare to read and store actual data in struct
		{
			if (temp == "dec")
			{
				variants = VARIANTS::PCF_ADRESSE;
				temp.clear();
			}
			else if (temp == "p")
			{
				variants = VARIANTS::PORT;
				temp.clear();
			}
			
		}

		if (single_character == "{")
		{
			object_name = temp;
			temp.clear();
		}
		if (single_character == ",")
		{
			switch (variants)
			{
			
			case VARIANTS::PCF_ADRESSE:
			{
				m_io_object.PCF8574_adresse = std::stoi(temp);
				temp.clear();
			}break;
			case VARIANTS::PORT:
			{
				m_io_object.PCF_8574_port = std::stoi(temp);
				temp.clear();
			}
			default:
				break;
			}
		}
		if (single_character == "}")//The last number doesn't have a comma following, so it has to be read when the bracelet is found
		{
			m_io_object.PCF_8574_port = std::stoi(temp);
			temp.clear();
			m_io_object.is_active = false;
			m_PCF8574_DigitalIn_Adresse_collection.insert({ object_name, m_io_object });
		}


	}

}

void HW_Con::loadAnalogInputAdresses(std::string path)
{
	std::string temp;
	std::string single_character;
	std::string object_name;

	enum struct VARIANTS { PCF_ADRESSE = 0, PORT = 1 } variants;

	std::ifstream object_position_file(m_getProjectDirPath() + path);
	object_position_file.seekg(0, object_position_file.end);
	int length = object_position_file.tellg();
	object_position_file.seekg(0, object_position_file.beg);

	char* buffer = new char[length];

	m_p_logger->writeLog(LogLevel::INFO, m_log_origin + " LOAD_ANALOGINPUT_DATA", "Reading: " + std::to_string(length) + " characters");

	object_position_file.read(buffer, length);

	object_position_file.close();

	//Unsafe, file could be corrupted!!
	for (int i = 0; i < length; i++)
	{
		single_character = buffer[i];

		if (single_character != "#" && single_character != "{" && single_character != "}" && single_character != "," && single_character != "\n" && single_character != "\r")
		{
			temp.append(single_character);
		}

		//Check if a variant code word had been read (dec for PCF8574 7-Bit Adresse, p for the Port). If yes clear string and prepare to read and store actual data in struct
		{
			if (temp == "dec")
			{
				variants = VARIANTS::PCF_ADRESSE;
				temp.clear();
			}
			else if (temp == "p")
			{
				variants = VARIANTS::PORT;
				temp.clear();
			}

		}

		if (single_character == "{")
		{
			object_name = temp;
			temp.clear();
		}
		if (single_character == ",")
		{
			switch (variants)
			{

			case VARIANTS::PCF_ADRESSE:
			{
				m_io_object.PCF8574_adresse = std::stoi(temp);
				temp.clear();
			}break;
			case VARIANTS::PORT:
			{
				m_io_object.PCF_8574_port = std::stoi(temp);
				temp.clear();
			}
			default:
				break;
			}
		}
		if (single_character == "}")//The last number doesn't have a comma following, so it has to be read when the bracelet is found
		{
			m_io_object.PCF_8574_port = std::stoi(temp);
			temp.clear();
			m_io_object.is_active = false;
			m_PCF8574_AnalogIn_Adresse_collection.insert({ object_name, m_io_object });
		}


	}

}
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

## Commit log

2025-11-22 .gitattributes und .gitignore hinzufügen.
2025-11-23 Added handling for object position file (position on display), improved comments from function prototypes in GUI.h
2025-11-29 Added Hardware Interface
    [A_In_config.txt, D_In_config.txt, D_Out_config.txt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]
2025-11-30 Added function to switch state of individual relays Added function to switch all relays of at startup of PCB and Software
2025-12-02 Enhance README with biogas plant diagram
    Added a schematic diagram to illustrate the function of the biogas plant.
2025-12-02 added hw_files
    [4_20_circuit_protection_.kicad_sch, Analog_Input.kicad_sch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]
2025-12-02 Added function to set the state of the relay directly. if the relay was already in that state, no I2C message is send
2025-12-30 added gpio pin reader
2026-01-04 added cursor movement with rotary encoder
2026-01-17 Improved sequence handling, current steps are now showable, added new function JUMP_TO
2026-01-17 Enhance README with motor control and function details
    Added details about motor control and pneumatic valves to the overview section. Expanded the function descriptions and added new functions for sequence control.
2026-02-01 beginn at reworking Sequence_Handler
    [main.cpp]
2026-02-07 reworked sequence_handler to no longer use std::map to organise the sequences. They are now stored in a vector and can be addressed by their position in in. However, a map is used to store the name o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
    [main.cpp]
2026-02-15 begin reworking sequence handler to be able to reload sequences
    [main.cpp]
2026-02-19 reworked sequence handler to be able to savely stop sequences and load new ones
    [main.cpp]
